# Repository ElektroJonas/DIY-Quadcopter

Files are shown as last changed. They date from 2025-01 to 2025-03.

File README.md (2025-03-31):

# Quadcopter Built from Scratch

This project contains all the materials used in building a quadcopter drone. It was part of a project course in electrical engineering and embedded systems at Uppsala University, where we spent a portion of the semester designing and constructing a quadcopter from scratch using off-the-shelf components and some interesting control algorithms! 🚀

### Project Demonstration and Summary
- A fun summary of the project's development can be found here: [YouTube Summary](https://youtu.be/-V470g73WhM?si=RAoppi26RXBP144A)  
- A demonstration of the drone can be found here: [YouTube Demonstration](https://youtu.be/1-YmHmeVQKA?si=Rilc_he6dhYzZJqS)  

### Final Result
Below is a figure of the completed drone and its custom-built remote control:

| Drone | Remote |  
| --- | --- |
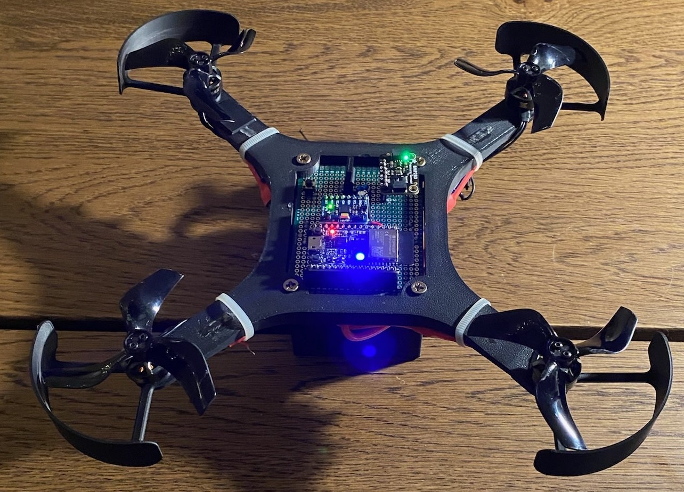
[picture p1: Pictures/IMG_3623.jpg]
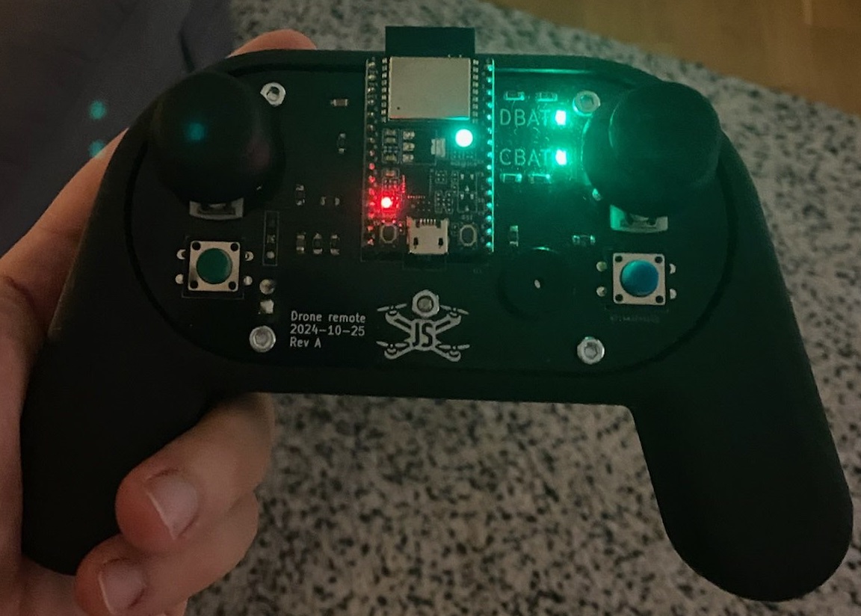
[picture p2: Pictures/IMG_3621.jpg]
|  |  |

### Control System  
The control system consists of two main components: **Attitude Control** and **Altitude Control**.  Note: Altitude control was not used in the final version of the drone since we didnt get it to work well enough.

- **Attitude Control** (angle relative to the ground plane) is implemented using a cascaded PID controller with a Kalman filter and an internal rate control loop. It relies on a low-cost MEMS sensor (gyroscope/accelerometer) for angle estimation.  
- **Altitude Control** is managed using a pressure sensor in combination with the MEMS sensor for attitude estimation, supplemented by a Zero Velocity Update (ZUPT) algorithm for improved stability and accuracy.   

The control system was implemented on an ESP32 microcontroller, utilizing the ESP-NOW protocol for wireless communication.

### Full Project Report
A detailed description of this project, including development insights, sources, and useful references for anyone interested in building their own drone, can be found in **Quadcopter_final_report.pdf**.

### Acknowledgments  
We would like to express our gratitude to [CarbonAeronautics](https://github.com/CarbonAeronautics) for providing valuable resources that greatly aided the early development of this project.  

A special thanks to **Uppsala University** for sponsoring the project and providing the opportunity to bring this idea to life!

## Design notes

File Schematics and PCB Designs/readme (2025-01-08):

The quadcopter has a schematic but currently no pcb design as it was realised on a experimental board. 
The remote has a schematic and pcb design. The pcb design can be improved further by adding 100nF capacitors on the ADC inputs to filter out noise

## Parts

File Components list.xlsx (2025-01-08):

Component | Articlenumber | Link | Quantity
ESP32C3 DevKit02 | ESP32-C3-DevKitC-02 | https://www.mouser.se/ProductDetail/Espressif-Systems/ESP32-C3-DevKitC-02?qs=stqOd1AaK7%2F1Q62ysr4CMA%3D%3D | 2
Propeller | N/A | https://droneit.se/product/gemfan-75mm-ducted-durable-3-blade-props-75mm-3-blade-2/ | 4
Motor | ECO14044800 | https://droneit.se/product/emax-eco-micro-1404-24s-cw/ | 4
MPU60-50 gyra/acc-sensor | SEN0142 | https://www.mouser.se/ProductDetail/DFRobot/SEN0142?qs=Zcin8yvlhnO0Rr0B1JJGiw%3D%3D | 1
ESC 12A | 9351000122-0 | https://hobbyking.com/en_us/turnigy-plush-32-12a-2-4s-brushless-speed-controller-w-bec-rev1-1-0.html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 | 4
microB kabel 1m | 41009860 | https://www.electrokit.com/usb-kabel-a-hane-micro-b-5p-hane-1m | 2
Joystick 10k | 41003708 | https://www.electrokit.com/joystick-10k-tummanovrering | 2
BMP280 | 41013962 | https://www.electrokit.com/temperatur-och-lufttryckssensor-pa-kort-bmp280 | 1
Button PCB 12x12mm - 4-pack | 41016089 | https://www.electrokit.com/tryckknapp-pcb-12x12mm-4-pack | 1
Aktiv piezosummer 85dB 3-16VDC PCB miniatyr | 41003599 | https://www.electrokit.com/summer-4-khz-miniatyr | 1
Hylslist 2.54mm 1x10p | 41002451 | https://www.electrokit.com/hylslist-2.54mm-1x10p | 2
Hylslist 2.54mm 1x5p | 41002449 | https://www.electrokit.com/hylslist-2.54mm-1x5p | 4
1206 X7R 1uF | 40503060 | https://www.electrokit.com/kondensator-1206-x7r-1uf-1025v | 10
1206 100nF | 40503054 | https://www.electrokit.com/kondensator-1206-x7r-100nf-10 | 10
Skjutomkopplare 1-pol on-on pcb vinklad | 41011898 | https://www.electrokit.com/skjutomkopplare-1-pol-on-on-pcb-vinklad | 2
10kohm SMD 1206 | 40818410 | https://www.electrokit.com/motstand-10kohm-0.25w-smd-1206 | 20
390ohm SMD 1206 | 40818239 | https://www.electrokit.com/motstand-390ohm-0.25w-smd-1206 | 10
100ohm SMD 1206 | 40818210 | https://www.electrokit.com/motstand-100ohm-0.25w-smd-1206 | 10
MPU-6050 accelerometer 3-axel & gyro monterad på kort | 41016233 | https://www.electrokit.com/mpu-6050-accelerometer-3-axel-gyro-monterad-pa-kort | 1
KA78R05CTU TO-220 5V 1A | 41013217 | https://www.electrokit.com/ka78r05ctu-to-220-5v-1a | 1
Vapex Li-Po Batteri 3S 11,1V 1300mAh 30C T-kontakt | VPLP014FD | https://www.batteriexperten.com/sv/artiklar/vapex-li-po-batteri-3s-111v-1300mah-30c-t-kontakt.html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 | 1
SkyRC e3-V2 2-3S LiPo XH Laddare 240VAC | SkyRC_e3-V2 | SkyRC e3-V2 2-3S LiPo XH Laddare 240VAC | 1

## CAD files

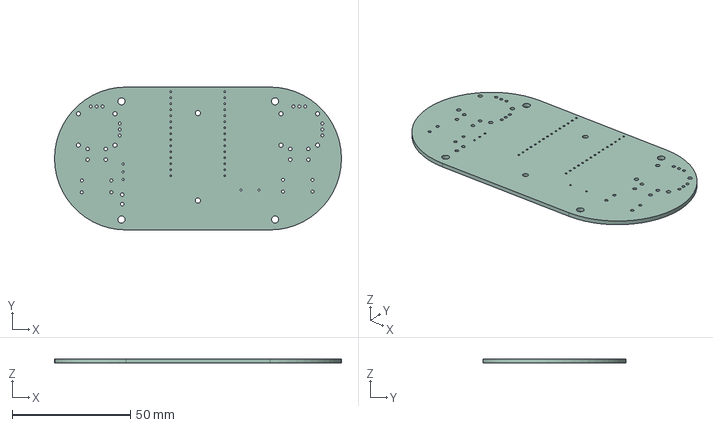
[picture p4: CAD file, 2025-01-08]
Schematics and PCB Designs/Remote/Remote.step
121.5 x 60.5 x 1.60 mm

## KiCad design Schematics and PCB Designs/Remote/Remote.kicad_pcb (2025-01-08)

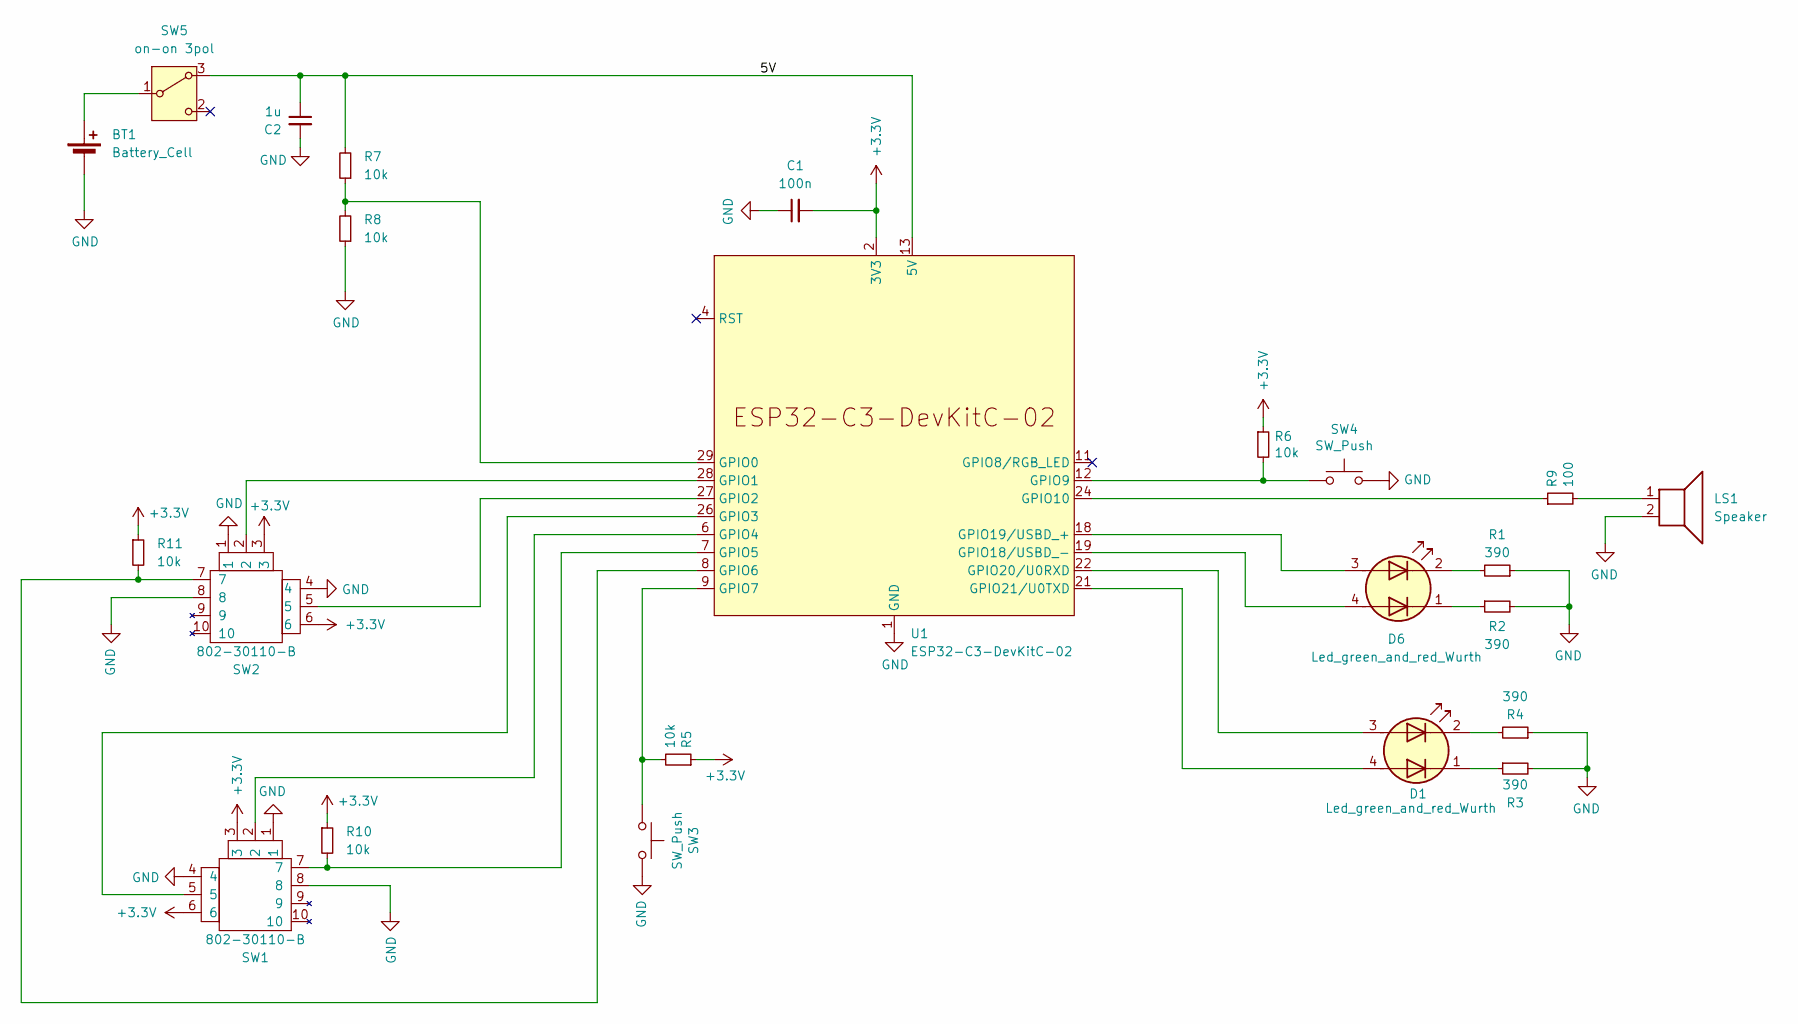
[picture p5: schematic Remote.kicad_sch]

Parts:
BT1: Battery_Cell; Batterihållare 4xAAA
C1: 100n; C_1206_3216Metric_Pad1.33x1.80mm_HandSolder
C2: 1u; C_1206_3216Metric_Pad1.33x1.80mm_HandSolder
D1, D6: Led_green_and_red_Wurth; Led green and red Wurth
LS1: Speaker; summer 4khz miniatyr
R1, R2, R3, R4: 390; R_1206_3216Metric_Pad1.30x1.75mm_HandSolder
R5, R6, R7, R8, R10, R11: 10k; R_1206_3216Metric_Pad1.30x1.75mm_HandSolder
R9: 100; R_1206_3216Metric_Pad1.30x1.75mm_HandSolder
SW1, SW2: 802-30110-B; Joystick
SW3, SW4: SW_Push; SW_PUSH-12mm
SW5: on-on 3pol; Skjutomkopplare 1-pol on-on pcb vinklad
U1: ESP32-C3-DevKitC-02

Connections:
5V: C2.1, R7.2, SW5.3 (A), U1.13 (5V), U1.14 (5V)
+3.3V: C1.2, R5.1, R6.1, R10.1, R11.1, SW1.3, SW1.6, SW2.3, SW2.6, U1.2 (3V3), U1.3 (3V3)
GND: BT1.2 (-), C1.1, C2.2, LS1.2, R1.1, R2.2, R3.2, R4.1, R8.1, SW1.1, SW1.4, SW1.8, SW2.1, SW2.4, SW2.8, SW3.2, SW4.2, U1.1 (GND), U1.5 (GND), U1.10 (GND), U1.15 (GND), U1.16 (GND), U1.17 (GND), U1.20 (GND), U1.23 (GND), U1.25 (GND), U1.30 (GND)
unnamed: BT1.1 (+), SW5.1 (B)
unnamed: D1.3 (A1), U1.22 (GPIO20/U0RXD)
unnamed: D1.4 (A2), U1.21 (GPIO21/U0TXD)
unnamed: D1.2 (K1), R4.2
unnamed: D1.1 (K2), R3.1
unnamed: D6.3 (A1), U1.18 (GPIO19/USBD_+)
unnamed: D6.4 (A2), U1.19 (GPIO18/USBD_-)
unnamed: D6.2 (K1), R1.2
unnamed: D6.1 (K2), R2.1
unnamed: LS1.1, R9.2
unnamed: R7.1, R8.2, U1.29 (GPIO0)
unnamed: SW2.2, U1.28 (GPIO1)
unnamed: SW2.5, U1.27 (GPIO2)
unnamed: SW1.5, U1.26 (GPIO3)
unnamed: SW1.2, U1.6 (GPIO4)
unnamed: R10.2, SW1.7, U1.7 (GPIO5)
unnamed: R11.2, SW2.7, U1.8 (GPIO6)
unnamed: R5.2, SW3.1, U1.9 (GPIO7)
unnamed: R6.2, SW4.1, U1.12 (GPIO9)
unnamed: R9.1, U1.24 (GPIO10)

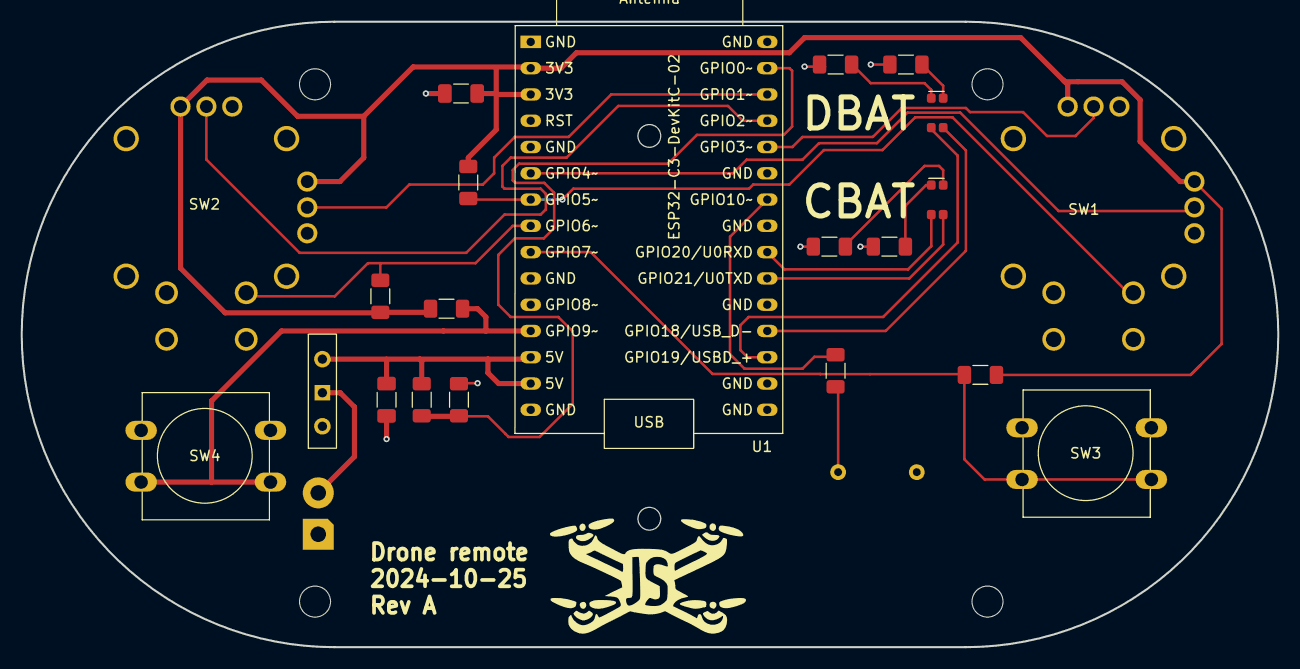
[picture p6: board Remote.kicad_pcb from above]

Board: 2 copper layers, 121.5 x 60.5 mm, 23 parts (1 on the bottom side), 23 nets.

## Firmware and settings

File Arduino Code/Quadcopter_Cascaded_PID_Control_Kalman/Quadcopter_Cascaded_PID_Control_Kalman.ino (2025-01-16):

/* 
  This code implements the control algorithm for a quadcopter drone on an ESP32, 
  including a cascaded PID controller and a Kalman filter for angle estimation. 
  It also uses ESP-NOW for wireless communication. 
  The theoretical background is described in the report at: https://github.com/ElektroJonas/Quadcopter-Control
  Created in 2024 by Jonas Gartner and Sigge Axelsson at Uppsala University in Sweden.
*/
#include "MPU6050.h"
#include <EEPROM.h>
#include "Wire.h"
#include "ESP32_NOW.h"
#include "WiFi.h"
#include <esp_mac.h>
#include <vector>

// -------------------- Wifi Config --------------------
#define ESPNOW_WIFI_CHANNEL 6
bool data_available = false;
unsigned long lastTransmission = 0;
uint32_t received_data;

class ESP_NOW_Peer_Class : public ESP_NOW_Peer {
public:
  ESP_NOW_Peer_Class(const uint8_t* mac_addr, uint8_t channel, wifi_interface_t iface, const uint8_t* lmk)
    : ESP_NOW_Peer(mac_addr, channel, iface, lmk) {}

  ~ESP_NOW_Peer_Class() {}

  bool add_peer() {
    if (!add()) {
      log_e("Failed to register the broadcast peer");
      return false;
    }
    return true;
  }

  void onReceive(const uint8_t* data, size_t len, bool broadcast) {
    received_data = *((uint32_t*)data);
    data_available = true;
  }

  // Public wrapper method to call the protected send()
  size_t sendData(const uint8_t* data, int len) {
    return send(data, len);
  }
};
std::vector<ESP_NOW_Peer_Class> masters;

void register_new_master(const esp_now_recv_info_t* info, const uint8_t*, int, void*) {
  if (memcmp(info->des_addr, ESP_NOW.BROADCAST_ADDR, 6) == 0) {
    Serial.printf("Unknown peer " MACSTR " sent a broadcast message\n", MAC2STR(info->src_addr));
    Serial.println("Registering the peer as a master");
    ESP_NOW_Peer_Class new_master(info->src_addr, ESPNOW_WIFI_CHANNEL, WIFI_IF_STA, NULL);
    masters.push_back(new_master);
    if (!masters.back().add_peer()) Serial.println("Failed to register the new master");
  } else Serial.printf("Received a unicast message from " MACSTR ", ignoring.\n", MAC2STR(info->src_addr));
}

// -------------------- Pins --------------------
const int M1 = 4, M2 = 5, M3 = 6, M4 = 7;
const int SDA_pin = 9, SCL_pin = 10;
const int batMeasPin = 1, calibratePin = 0;

// -------------------- Sensor Variables --------------------
MPU6050 accelgyro;
int16_t ax, ay, az, gx, gy, gz;
float axS, ayS, azS, gxS, gyS, gzS;
float angleAccelX, angleAccelY, denomX, denomY;
float gyroscopeRes, accelerationRes;
int16_t offsets[6];

// -------------------- Timing & PWM --------------------
const int freq = 250, resolution = 14;
unsigned long lastUpdateCool = millis(), lastKalmanUpdate = micros(), lastUpdate = micros(), lastBatMeasurement = millis(), now = micros(), lastCriticalVoltage = millis();
float dt, dt_kalman;
const unsigned long loopTime = 1000000 / freq;
const unsigned long loopTimeKalman = loopTime / 4;

// -------------------- Motor & Control --------------------
float P1 = 0, P2 = 0, P3 = 0, P4 = 0;
int PCOM = 0, PDIFF_x = 0, PDIFF_y = 0, PDIFF_z = 0;
bool motorsOn = false;
bool hold = false;
bool criticalVoltage = false;
float batteryVoltage;
uint8_t throttle;

// PID variables ANGLE (X/Y)
float refXAng = 0, e_x_prev_angle = 0, P_x_angle = 0, I_x_angle = 0, D_x_angle = 0;
float refYAng = 0, e_y_prev_angle = 0, P_y_angle = 0, I_y_angle = 0, D_y_angle = 0;

// PID variables RATE (X/Y/Z)
float refXRate = 0, e_x_prev_rate = 0, P_x_rate = 0, I_x_rate = 0, D_x_rate = 0;
float refYRate = 0, e_y_prev_rate = 0, P_y_rate = 0, I_y_rate = 0, D_y_rate = 0;
float refZRate = 0, e_z_prev_rate = 0, P_z_rate = 0, I_z_rate = 0, D_z_rate = 0;

// PID Coefficients
float Kp_angle = 0.4, Ki_angle = 0, Kd_angle = 0;
float Kp_rate = 0.7, Ki_rate = 2.5, Kd_rate = 0.02;
float Kp_z_rate = 1, Ki_z_rate = 4, Kd_z_rate = 0;

// Kalman Variables
float KalmanAngleRoll = 0, KalmanUncertaintyAngleRoll = 0;
float KalmanAnglePitch = 0, KalmanUncertaintyAnglePitch = 0;
float Q_angle, R_measure;

// -------------------- Functions --------------------
void rgb(int r, int g, int b) {
  neopixelWrite(RGB_BUILTIN, r, g, b);
}

void setParamsSerial(float& Kp, float& Ki, float& Kd) {
  unsigned long timer = millis();
  while (!Serial.available()) {
    if (millis() - timer >= 10000) {  // Safe timeout handling
      Serial.println("Timeout: No parameters received.");
      Serial.printf("Using standard parameters: Kp,Ki,Kd = %.2f,%.2f,%.2f\n", Kp, Ki, Kd);
      return;
    }
  }

  String input = Serial.readStringUntil('\n');
  input.trim();
  uint8_t vals[3];
  int n = sscanf(input.c_str(), "%hhu,%hhu,%hhu", &vals[0], &vals[1], &vals[2]);
  if (n == 3) {
    Kp = (float)vals[0] / 10;
    Ki = (float)vals[1] / 10;
    Kd = (float)vals[2] / 100;
    Serial.printf("Updated, Kp,Ki,Kd = %.2f,%.2f,%.2f\n", Kp, Ki, Kd);
  } else Serial.println("Error: Send 3 values as 10*Kp, 10*Ki, 100*Kd (0-255)");
}

void setPulseWidth(int pin, int pw, int limit = 2000) {
  pw = min(pw, limit);
  int dutyCycle = (pw * ((1 << resolution) - 1)) / loopTime;
  ledcWrite(pin, dutyCycle);
}

void getTransmission() {
  if (!data_available) return;
  lastTransmission = millis();
  throttle = (received_data >> 24) & 0xFF;
  throttle = (throttle > 55) ? throttle - 55 : 0;
  if(!hold) PCOM = map(throttle, 0, 200, 1300, 1600); //Joystick 0 position equals 138-50 => 1440 throttle
  refXAng = (float)((received_data >> 8) & 0xFF) - 138; //Sensor rotated by 90deg in late stage so refx becomes refy, therefore we shift by 8 instead of 16
  refXAng = (refXAng > -5 && refXAng < 5) ? 0 : refXAng;
  refXAng /= -4;

  refYAng = (float)((received_data >> 16) & 0xFF) - 138;
  refYAng = (refYAng > -5 && refYAng < 5) ? 0 : refYAng;
  refYAng /= 4;

  refZRate = (float)((received_data >> 4) & 0x0F) - 8;
  refZRate = (refZRate > -1 && refZRate < 1) ? 0 : refZRate*8; //Max roration rate will be 4*8 32deg/s

  if ((received_data >> 3) & 0x01) {
    EEPROM.write(0, 1);
    EEPROM.commit();
    delay(10);
    ESP.restart();
  }
  motorsOn = (received_data >> 2) & 0x01;
  hold = (received_data >> 1) & 0x01;
  data_available = false;
}

void calibrateMPU6050() {
  Serial.println("Old offsets:");
  accelgyro.PrintActiveOffsets();
  accelgyro.CalibrateAccel(20);
  accelgyro.CalibrateGyro(20);
  Serial.println("\nCalibration Successful! \nNew offsets:");
  accelgyro.PrintActiveOffsets();
  int16_t* ao = accelgyro.GetActiveOffsets();
  for (int i = 0; i < 6; i++) offsets[i] = ao[i];
  EEPROM.put(1, offsets);
  EEPROM.commit();
}

void setEEpromOffsets() {
  EEPROM.get(1, offsets);
  accelgyro.setXAccelOffset(offsets[0]);
  accelgyro.setYAccelOffset(offsets[1]);
  accelgyro.setZAccelOffset(offsets[2]);
  accelgyro.setXGyroOffset(offsets[3]);
  accelgyro.setYGyroOffset(offsets[4]);
  accelgyro.setZGyroOffset(offsets[5]);
  Serial.println("Offsets set:");
  accelgyro.PrintActiveOffsets();
}

void escSetup() {
  const int motors[] = { M1, M2, M3, M4 };
  for (int m : motors) setPulseWidth(m, 2400, 2400);
  delay(4000);
  for (int m : motors) setPulseWidth(m, 900);
  delay(4000);
}

float calculatePID(float ref, float y, float& e_prev, float& P, float& I, float& D, float Kp, float Ki, float Kd, float dt, int Icap = 400) {
  float e = ref - y;
  P = Kp * e;
  I += Ki * (e + e_prev) * dt;
  I = constrain(I, -Icap, Icap);
  D = Kd * (e - e_prev) / dt;
  e_prev = e;
  return P + I + D;
}

void plotCool(unsigned long currentTime) { //Used for debugging
  if (currentTime - lastUpdateCool >= loopTime * 50) {
    lastUpdateCool = currentTime;
    //Serial.printf("P_x:%.3f,", P_x_rate);
    //Serial.printf("I_x:%.3f,", I_x_rate);
    //Serial.printf("D_x:%.3f,", D_x_rate);

    //Serial.printf("P_y:%.3f,", P_y_rate);
    //Serial.printf("I_y:%.3f,", I_y_rate);
    //Serial.printf("D_y:%.3f,", D_y_rate);

    //Serial.printf("P_z:%.3f,", P_z_rate);
    //Serial.printf("I_z:%.3f,", I_z_rate);
    //Serial.printf("D_z:%.3f,", D_z_rate);

    //Serial.printf("angleAccelX:%.3f,", angleAccelX);
    Serial.printf("Kalman_Angle_X:%.3f,", KalmanAngleRoll);
    Serial.printf("Kalman_Angle_y:%.3f,", KalmanAnglePitch);
    //Serial.printf("axS:%.3f,", axS);
    //Serial.printf("ayS:%.3f,", ayS);
    //Serial.printf("azS:%.3f,", azS);
    //Serial.printf("gxS:%.3f,", gxS);
    //Serial.printf("gyS:%.3f,", gyS);
    //Serial.printf("gzS:%.3f\n", gzS);
    float v = analogRead(batMeasPin);
    Serial.printf("Voltage:%.3f\n", batteryVoltage); //(measurement/2^8)((3300 + 220)/220)*1.18 = measurement/adcres*(voltage division)*measuredADCREF
    Serial.printf("VoltageRaw:%.3f\n", v);
    
  }
}

void kalman_1d(float& x, float& P, float u, float y, float Q, float R, float G, float F, float H) {
  x = F * x + G * u;  // Predictions
  P = F * P * F + Q;
  float y_tilde = y - H * x;  // Updates
  float S = H * P * H + R;
  float K = P * H / S;
  x += K * y_tilde;
  P -= K * H * P;
}

// ============================== SETUP ==============================
void setup() {
  pinMode(calibratePin, INPUT);
  Serial.begin(115200);
  analogReadResolution(12);
  analogSetAttenuation(ADC_2_5db);
  Wire.begin(SDA_pin, SCL_pin);
  Wire.setClock(200000);
  EEPROM.begin(16);  // initialize EEPROM (flash memory for esp32) with predefined size
  rgb(10, 10, 0);    // LED indicate config

  // Configure PWM & ESC
  if (ledcAttach(M1, freq, resolution) && ledcAttach(M2, freq, resolution) && ledcAttach(M3, freq, resolution) && ledcAttach(M4, freq, resolution))
    Serial.println("PWM setup successful");
  else {
    Serial.println("PWM setup failed\nRebooting in 5 seconds...");
    rgb(20, 0, 0);
    delay(5000);
    ESP.restart();
  }
  
  // Initialize MPU6050
  accelgyro.initialize();                     // Arguments are the range: A2G= ±2g, G2000DPS = ±2000deg/s
  accelgyro.setFullScaleGyroRange(0x03);      // Full Scale Range: ±2000°/s
  accelgyro.setFullScaleAccelRange(0x01);     // Full Scale Range: ±4g
  accelgyro.setDLPFMode(MPU6050_DLPF_BW_10);  // Low-Pass filter: MPU6050_DLPF_BW_10 = Bandwidth 10Hz
  gyroscopeRes = 2000.0 / 32768.0;            // Adjust based on setFullScaleGyroRange!escset
  accelerationRes = 4.0 / 32768.0;            // Adjust based on setFullScaleAccelRange!

  if (!accelgyro.testConnection()) {
    Serial.println("MPU6050 connection failed\nRebooting in 5 seconds...");
    delay(5000);
    ESP.restart();
  }
  Serial.println("MPU6050 connection successful!");

  for (int i = 0; i < 200; i++) {
    delay(10);
    if (!digitalRead(calibratePin)) {
      Serial.print("Calibration Button pressed B)");
      escSetup();
      break;
    }
  }

  // Sensor Calibration
  if (EEPROM.read(0)) {
    Serial.println("Performing calibration...");
    calibrateMPU6050();
    setEEpromOffsets();
    EEPROM.write(0, 0);
    EEPROM.commit();
  } else setEEpromOffsets();

  Serial.println("Initializing Wi-Fi");
  WiFi.mode(WIFI_STA);
  WiFi.setChannel(ESPNOW_WIFI_CHANNEL);
  while (!WiFi.STA.started()) delay(100);
  if (!ESP_NOW.begin()) {
    Serial.println("Failed to initialize ESP-NOW\nRebooting in 5 seconds...");
    rgb(20, 0, 0);
    delay(5000);
    ESP.restart();
  }
  ESP_NOW.onNewPeer(register_new_master, NULL);
  Serial.println("Wifi setup complete");

  // Set Parameters With Serial Monitor
  //Serial.println("\n[RATE] Send rate roll/pitch parameters as K_p,K_i,K_d:");
  setParamsSerial(Kp_rate, Ki_rate, Kd_rate);
  //Serial.println("\n[RATE] Send rate yaw parameters as K_p,K_i,K_d:");
  setParamsSerial(Kp_z_rate, Ki_z_rate, Kd_z_rate);
  Serial.println("\n[ANGLE] Send angle roll/pitch parameters as K_p,K_i,K_d:");
  setParamsSerial(Kp_angle, Ki_angle, Kd_angle);
  Serial.println("\nParameters Set!");

  rgb(0, 0, 20);  // LED indicate config complete
}


// ============================== LOOP ==============================
void loop() {
  //Battery measurement
  now = millis();
  if (now - lastBatMeasurement >= 50 && now - lastCriticalVoltage >= 5000) {
    lastBatMeasurement = now;
    batteryVoltage = analogRead(batMeasPin)*0.00457;                                //(measurement/(2^12-1))((3300 + 220)/220)*1.19 = measurement/adcres*(voltage division)*measuredADCRef
    uint32_t message = batteryVoltage*1000;                                         //Multiply by 1000 to avoid floating point issues
    if (!masters.empty()) masters[0].sendData((uint8_t*)&message, sizeof(message)); //Send drone voltage to remote
    if (batteryVoltage < 9.4){
      criticalVoltage = true;
      lastCriticalVoltage = now;
    }
    else criticalVoltage = false;
  }


  // Kalman loop (fast)
  now = micros();
  if (now - lastKalmanUpdate >= loopTimeKalman) {
    getTransmission();
    dt_kalman = (now - lastKalmanUpdate) * 1e-6f;
    lastKalmanUpdate = now;

    accelgyro.getMotion6(&ax, &ay, &az, &gx, &gy, &gz);
    axS = ax * accelerationRes;
    ayS = ay * accelerationRes;
    azS = az * accelerationRes;
    gxS = gx * gyroscopeRes;
    gyS = gy * gyroscopeRes;
    gzS = gz * gyroscopeRes;

    denomX = sqrtf(axS * axS + azS * azS);
    denomX = denomX > 1e-6f ? denomX : 1e-6f;
    denomY = sqrtf(ayS * ayS + azS * azS);
    denomY = denomY > 1e-6f ? denomY : 1e-6f;
    angleAccelX = atan2f(ayS, denomX) * RAD_TO_DEG;
    angleAccelY = -atan2f(axS, denomY) * RAD_TO_DEG;

    Q_angle = 3 * dt_kalman * dt_kalman;
    R_measure = 12;
    kalman_1d(KalmanAngleRoll, KalmanUncertaintyAngleRoll, gxS, angleAccelX, Q_angle, R_measure, dt_kalman, 1, 1);
    kalman_1d(KalmanAnglePitch, KalmanUncertaintyAnglePitch, gyS, angleAccelY, Q_angle, R_measure, dt_kalman, 1, 1);
    KalmanAngleRoll = constrain(KalmanAngleRoll, -45, 45);
    KalmanAnglePitch = constrain(KalmanAnglePitch, -45, 45);
  }

  // Control loop (limited by ESC frequency)
  now = micros();
  if (now - lastUpdate >= loopTime) {
    dt = (now - lastUpdate) * 1e-6f;
    lastUpdate = now;

    // ANGLE PID
    refXRate = calculatePID(refXAng, KalmanAngleRoll, e_x_prev_angle, P_x_angle, I_x_angle, D_x_angle, Kp_angle, Ki_angle, Kd_angle, dt);
    refYRate = calculatePID(refYAng, KalmanAnglePitch, e_y_prev_angle, P_y_angle, I_y_angle, D_y_angle, Kp_angle, Ki_angle, Kd_angle, dt);

    // RATE PID
    PDIFF_x = calculatePID(refXRate, gxS, e_x_prev_rate, P_x_rate, I_x_rate, D_x_rate, Kp_rate, Ki_rate, Kd_rate, dt);
    PDIFF_y = calculatePID(refYRate, gyS, e_y_prev_rate, P_y_rate, I_y_rate, D_y_rate, Kp_rate, Ki_rate, Kd_rate, dt);
    PDIFF_z = calculatePID(refZRate, gzS, e_z_prev_rate, P_z_rate, I_z_rate, D_z_rate, Kp_z_rate, Ki_z_rate, Kd_z_rate, dt);

    // Compute motor power
    if (!criticalVoltage){ //Battery voltage at stable levels    
      P1 = PCOM + PDIFF_x - PDIFF_y + PDIFF_z;
      P2 = PCOM - PDIFF_x - PDIFF_y - PDIFF_z;
      P3 = PCOM + PDIFF_x + PDIFF_y - PDIFF_z;
      P4 = PCOM - PDIFF_x + PDIFF_y + PDIFF_z;
    }
    else //Battery voltage at critical levels
    {
      P1 = 1400 + PDIFF_x/2 - PDIFF_y/2 + PDIFF_z/2;
      P2 = 1400 - PDIFF_x/2 - PDIFF_y/2 - PDIFF_z/2;
      P3 = 1400 + PDIFF_x/2 + PDIFF_y/2 - PDIFF_z/2;
      P4 = 1400 - PDIFF_x/2 + PDIFF_y/2 + PDIFF_z/2;
    }


    if (!motorsOn) {
      rgb(0, 0, 20);
      P1 = P2 = P3 = P4 = 900;  // Minimum pulse width
      P_x_rate = I_x_rate = D_x_rate = 0;
      P_y_rate = I_y_rate = D_y_rate = 0;
      P_z_rate = I_z_rate = D_z_rate = 0;
      P_x_angle = I_x_angle = D_x_angle = 0;
      P_y_angle = I_y_angle = D_y_angle = 0;
    } else rgb(0, 20, 0);

    setPulseWidth(M1, (int)P1);
    setPulseWidth(M2, (int)P2);
    setPulseWidth(M3, (int)P3);
    setPulseWidth(M4, (int)P4);

    plotCool(now);
  }
}

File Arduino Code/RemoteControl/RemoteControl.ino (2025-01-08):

#include <esp_now.h>
#include <WiFi.h>
#include <esp_mac.h>  // For the MAC2STR and MACSTR macros

// ==================== CONFIGURATION ====================
#define ESPNOW_WIFI_CHANNEL 6

// Pin definitions
const int joyLX = 2;
const int joyLY = 1;
const int joyRX = 3;
const int joyRY = 4;
const int joyLC = 6;
const int joyRC = 5;
const int buttL = 9;
const int buttR = 7;
const int speaker = 10;
const int cBatRed = 21;
const int cBatGreen = 20;
const int dBatRed = 18;
const int dBatGreen = 19;
const int batMeas = 0;

// Variables
int timer1 = 0;
int timer2 = 0;
bool beepFlag = true;
bool motorsOn = false;
uint32_t data;
bool mute = false;

// Transmission variables
uint8_t throttle = 0;
uint8_t ref_x = 0;
uint8_t ref_y = 0;
uint8_t ref_z = 0;
bool calibration = false;
bool hold = false;
bool unused2 = false;

// Reception variables
float droneBatteryLevel = 12.0;
bool data_avaliable = false;

// Define broadcast address (all 0xFF)
uint8_t broadcastAddress[6] = {0xFF,0xFF,0xFF,0xFF,0xFF,0xFF};

// Forward declaration of functions
void rgb(int r, int g, int b);
void beep(bool beep);
void checkDroneBattery();
float checkControllerBattery();
bool transmit();

void onDataReceive(const esp_now_recv_info_t *info, const uint8_t *data, int len)
{
  if (len == sizeof(uint32_t)) 
  {
    droneBatteryLevel = (float)*((uint32_t*)data)/1000.0; //We multiply by 1000 before sending so that we can represent our 3 decimal float as a uint32_t
  }
}

void rgb(int r, int g, int b) {
  neopixelWrite(RGB_BUILTIN, r, g, b);  //values 0 to 255
}

void setup() {
  analogReadResolution(8);

  pinMode(buttL, INPUT);
  pinMode(buttR, INPUT);
  pinMode(speaker, OUTPUT);
  pinMode(joyLC, INPUT);
  pinMode(joyRC, INPUT);

  if(digitalRead(buttL) == LOW) { // Enter boot mode
    pinMode(cBatRed, INPUT);
    pinMode(cBatGreen, INPUT);
    pinMode(dBatRed, INPUT);
    pinMode(dBatGreen, INPUT);
    while(1){}; // Stuck here until reset
  } else {
    pinMode(cBatRed, OUTPUT);
    pinMode(cBatGreen, OUTPUT);
    pinMode(dBatRed, OUTPUT);
    pinMode(dBatGreen, OUTPUT);
  }

  // Initialize Wi-Fi
  WiFi.mode(WIFI_STA);
  WiFi.setChannel(ESPNOW_WIFI_CHANNEL);
  while (!WiFi.STA.started()) {
    delay(100);
  }

  Serial.println("Wi-Fi parameters:");
  Serial.println("  Mode: STA");
  Serial.println("  MAC Address: " + WiFi.macAddress());
  Serial.printf("  Channel: %d\n", ESPNOW_WIFI_CHANNEL);

  // Initialize ESP-NOW
  if (esp_now_init() != ESP_OK) {
    Serial.println("Failed to initialize ESP-NOW");
    Serial.println("Rebooting in 5 seconds...");
    delay(5000);
    ESP.restart();
  }

  // Register the receive callback
  esp_now_register_recv_cb(onDataReceive);

  // Add broadcast peer
  esp_now_peer_info_t peerInfo;
  memset(&peerInfo, 0, sizeof(peerInfo));
  memcpy(peerInfo.peer_addr, broadcastAddress, 6);
  peerInfo.channel = ESPNOW_WIFI_CHANNEL;
  peerInfo.encrypt = false;

  if (esp_now_add_peer(&peerInfo) != ESP_OK) {
    Serial.println("Failed to add broadcast peer");
    Serial.println("Rebooting in 5 seconds...");
    delay(5000);
    ESP.restart();
  }

  Serial.println("Setup complete.");
  rgb(2, 2, 2);
}

void beep(bool beepOn) {
  beepFlag = !beepFlag;
  if(mute)
  {
    digitalWrite(speaker,LOW);
    return;
  }
  else if (beepOn) {
    digitalWrite(speaker,beepFlag);
  } else {
    digitalWrite(speaker,LOW);
  }
}

void checkDroneBattery() {
  if (droneBatteryLevel < 9.4) {
    digitalWrite(dBatRed,beepFlag); // Use beepFlag to blink
    digitalWrite(dBatGreen,LOW);
    beep(true);
  } else if (droneBatteryLevel < 11.5) {
    digitalWrite(dBatRed,HIGH);
    digitalWrite(dBatGreen,HIGH);
    beep(false);
  } else {
    digitalWrite(dBatRed,LOW);
    digitalWrite(dBatGreen,HIGH);
    beep(false);
  }
}

float checkControllerBattery() {
  float voltage = 2 * analogRead(batMeas) * (3.3/255); // Adjust based on actual circuit
  if (voltage < 4.4) {
    digitalWrite(cBatRed,beepFlag);
    digitalWrite(cBatGreen,LOW);
    beep(true);
  } else if (voltage < 5.4) {
    digitalWrite(cBatRed,HIGH);
    digitalWrite(cBatGreen,HIGH);
    beep(false);
  } else {
    digitalWrite(cBatRed,LOW);
    digitalWrite(cBatGreen,HIGH);
    beep(false);
  }
  return voltage;
}

bool transmit() {
  data = ((throttle << 24) | (ref_x << 16) | (ref_y << 8) | 
           (ref_z & 0b11110000) | ((calibration ? 1 : 0) << 3) |
           ((motorsOn ? 1 : 0) << 2) | ((hold ? 1 : 0) << 1) | 
           (unused2 ? 1 : 0));

  esp_err_t result = esp_now_send(broadcastAddress, (uint8_t *)&data, sizeof(data));
  if (result != ESP_OK) {
    Serial.println("Failed to broadcast message");
    rgb(5,0,0);
    return false;
  } else {
    rgb(0,2,0);
    return true;
  }
}

void loop() {
  if(millis() > timer1 + 300) { // runs every 300ms
    checkControllerBattery();
    timer1 = millis();
  }
  if(millis() > timer2 + 50) { // runs every 100ms
    checkDroneBattery();
    timer2 = millis();
  }

  throttle = analogRead(joyLY);
  ref_x = analogRead(joyRY);
  ref_y = analogRead(joyRX);
  ref_z = analogRead(joyLX); // discard 4 LSBs later if needed

  calibration = !digitalRead(buttL); // active-low

  if(!digitalRead(joyLC)) { // toggles motors on/off
    motorsOn = !motorsOn;
    if(!motorsOn) hold = false; //We want to reset the hold variable when motors turn off
    delay(300); // debounce delay
  }

    if(!digitalRead(joyRC)) { // toggles hold on/off
    hold = !hold;
    delay(300); // debounce delay
  }

  if(!digitalRead(buttR))
  {
    mute = !mute;
    delay(200);
  }

  delay(10);
  transmit();
}

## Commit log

2025-01-08 Create Quadcopter_Cascaded_PID_Control_Kalman.ino
    Complete code to control a esp32 based quadcopter is inserted.
2025-01-08 Uploaded Schematics and PCB Designs
    Uploaded schematics for the quadcopter and remote, as well as a pcb design for the remote. The quadcopter does not yet have a custom made pcb.
    [Quadcopter.kicad_pcb, Quadcopter.kicad_sch, Remote.kicad_pcb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]
2025-01-08 Added arduino code for the remote control aswell as a components list
    [Components list.xlsx]
2025-03-12 Create Cad files
    Added link to onshape cad files for drone frame and remote
